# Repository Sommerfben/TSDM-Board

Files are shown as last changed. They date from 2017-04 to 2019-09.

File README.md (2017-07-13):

*Copyright UBC Formula Electric 2017.* 

*This documentation describes Open Hardware and is licensed under the CERN OHL v1.2.*

*You may redistribute and modify this documentation under the terms of the [CERN OHL v1.2](http://ohwr.org/cernohl). This documentation is distributed WITHOUT ANY EXPRESS OR IMPLIED WARRANTY, INCLUDING OF MERCHANTABILITY, SATISFACTORY QUALITY, AND FITNESS FOR A PARTICULAR PURPOSE. Please see the CERN OHL v1.2 for applicable conditions.*

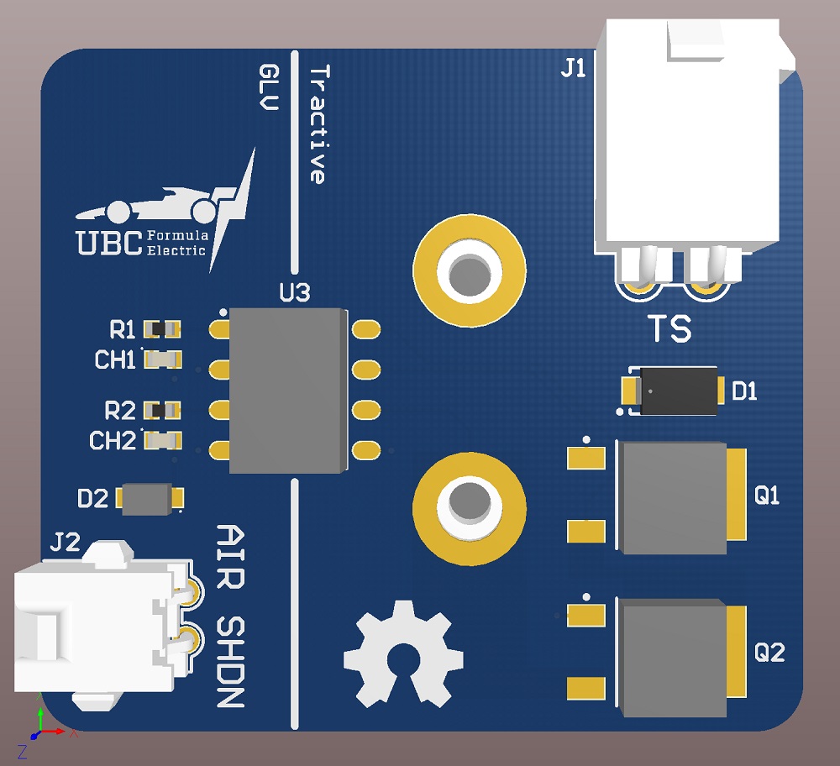
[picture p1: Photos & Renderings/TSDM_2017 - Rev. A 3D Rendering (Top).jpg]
TSDM_2017 - Rev. A 3D Render (Top)

*TSDM_2017 - Rev. A 3D Render (Top)*

# Overview

The Tractive System Discharge Module (TSDM_2017) discharges the tractive system in accordance with the 2017 Formula SAE rules. It uses two MOSFETs and a power resistor to discharge the repackaged inverter filtering capacitors below 60V in <1.5 seconds (to meet EV5.1.3). The power resistor is connected across the two poles of the tractive system whenever the AIR shutdown circuit is open, even when the vehicle is off.

# Features & Specifications

- The TSDM is separated into GLV (low-voltage) and tractive system (high-voltage) sections by a 10mm isolation boundary as per EV4.1.7. The GLV section contains the AIR shutdown circuit input and the tractive system section contains the MOSFETs and power resistor. The two halves are bridged by an optoisolated MOSFET driver.
- The board is mounted directly onto the power resistor using two M4 bolts. The power resistor is itself mounted to the inverter enclosure using two M3 studs and thermal compound. This design reduces the number of fasteners required for mounting and improves reliability by eliminating the use of additional wires and connectors.
- The AIR shutdown input uses a TE Micro MATE-N-LOK connector and is protected against reverse polarity by a Schottky diode and overcurrent by a PTC fuse. 
- The tractive system input uses a TE Mini-Universal MATE-N-LOK connector and is protected against reverse polarity by a 600V diode. Fusing is not allowed in the discharge circuit as per EV4.11.6.
- Each channel of the MOSFET driver has a red LED placed in series to provide a visual indicator of when the power resistor is disconnected from the tractive circuit.
- The power resistor is switched in and out of the system using two depletion-mode MOSFETs placed in series. The use of depletion-mode devices eliminates the need for conventional relays and allows the resistor to remain connected across the circuit when no power is applied to the system. The two MOSFETs are placed in series for redundancy, as a failure to discharge the tractive system quickly could pose a serious safety hazard when working on the vehicle.

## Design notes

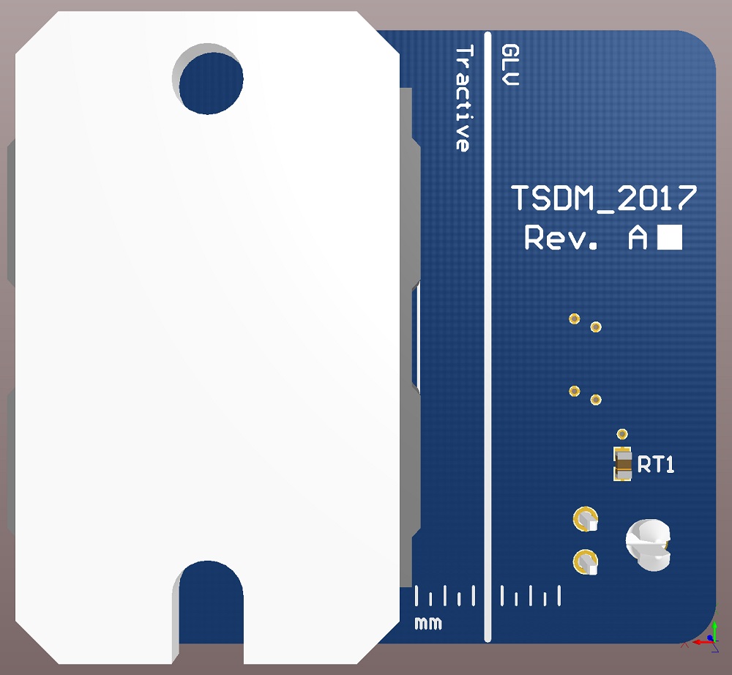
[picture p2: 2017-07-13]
Photos & Renderings/TSDM_2017 - Rev. A 3D Rendering (Bottom).jpg

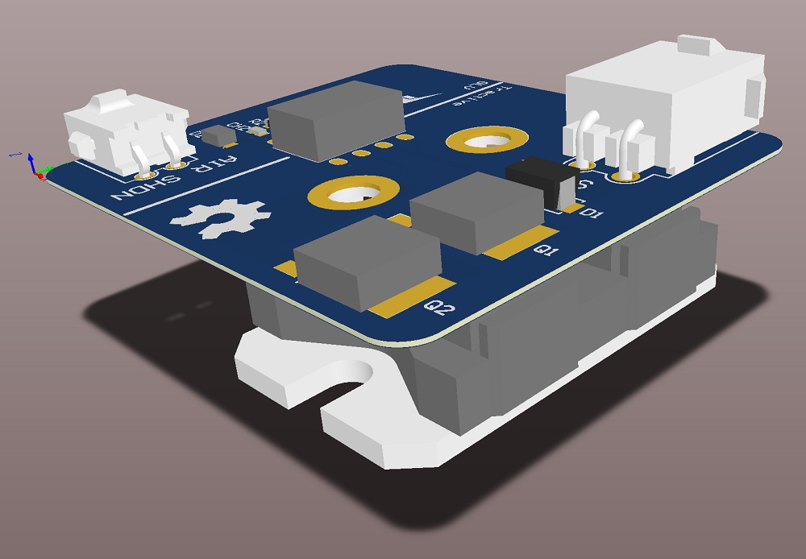
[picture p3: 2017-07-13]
Photos & Renderings/TSDM_2017 - Rev. A 3D Rendering (Isometric).jpg

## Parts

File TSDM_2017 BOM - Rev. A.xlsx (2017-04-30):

Description | Designator | Manufacturer | Manufacturer Part Number | Quantity | Supplier | Supplier Currency | Supplier Part Number | Supplier Order Qty | Supplier Unit Price | Supplier Subtotal
600V 1A Diode | D1 | STMicroelectronics (https://octopart-clicks.com/click/altium?sku=497-3765-1-ND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) | STTH1R06A (https://octopart-clicks.com/click/altium?sku=497-3765-1-ND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) | 1 | Digi-Key | CAD | 497-3765-1-ND (https://octopart-clicks.com/click/altium?sku=497-3765-1-ND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) | 1 | 0.65 | 0.65
60V 2A Schottky Diode | D2 | Nexperia USA Inc. (https://octopart-clicks.com/click/altium?sku=1727-2411-1-ND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) | PMEG6020AELRX (https://octopart-clicks.com/click/altium?sku=1727-2411-1-ND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) | 1 | Digi-Key | CAD | 1727-2411-1-ND (https://octopart-clicks.com/click/altium?sku=1727-2411-1-ND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) | 1 | 0.6 | 0.6
Green Chip LED | D3, D4 | Lite-On Inc. (https://octopart-clicks.com/click/altium?sku=160-1828-1-ND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) | LTST-C193KGKT-5A (https://octopart-clicks.com/click/altium?sku=160-1828-1-ND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) | 2 | Digi-Key | CAD | 160-1828-1-ND (https://octopart-clicks.com/click/altium?sku=160-1828-1-ND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) | 2 | 0.59 | 1.18
Mini-Universal MATE-N-LOK 2-Pin Female Connector | J1 | TE Connectivity AMP Connectors (https://octopart-clicks.com/click/altium?manufacturer=TE%20Connectivity%20AMP%20Connectors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) | 1-770966-0 (https://octopart-clicks.com/click/altium?manufacturer=TE%20Connectivity%20AMP%20Connectors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) | 1 | Digi-Key | CAD | A32471-ND (https://octopart-clicks.com/click/altium?manufacturer=TE%20Connectivity%20AMP%20Connectors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) | 1 | 1.27 | 1.27
Micro MATE-N-LOK 2-Pin Female Connector | J2 | TE Connectivity AMP Connectors (https://octopart-clicks.com/click/altium?manufacturer=TE%20Connectivity%20AMP%20Connectors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) | 2-1445055-2 (https://octopart-clicks.com/click/altium?manufacturer=TE%20Connectivity%20AMP%20Connectors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) | 1 | Digi-Key | CAD | A33207-ND (https://octopart-clicks.com/click/altium?manufacturer=TE%20Connectivity%20AMP%20Connectors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) | 1 | 1.11 | 1.11
500V Depletion-Mode N-MOSFET | Q1, Q2 | IXYS (https://octopart-clicks.com/click/altium?sku=IXTY1R6N50D2-ND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) | IXTY1R6N50D2 (https://octopart-clicks.com/click/altium?sku=IXTY1R6N50D2-ND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) | 2 | Digi-Key | CAD | IXTY1R6N50D2-ND (https://octopart-clicks.com/click/altium?sku=IXTY1R6N50D2-ND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) | 2 | 3.47 | 6.94
Thick Film Chip Resistor | R1, R2 | Panasonic Electronic Components (https://octopart-clicks.com/click/altium?manufacturer=Panasonic%20Electronic%20Components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) | ERJ-3EKF1001V (https://octopart-clicks.com/click/altium?manufacturer=Panasonic%20Electronic%20Components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) | 2 | Digi-Key | CAD | P1.00KHCT-ND (https://octopart-clicks.com/click/altium?manufacturer=Panasonic%20Electronic%20Components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) | 2 | 0.15 | 0.3
Thick Film Power Resistor | R3 | Ohmite (https://octopart-clicks.com/click/altium?sku=TGHLV1K00JE-ND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) | TGHLV1K00JE (https://octopart-clicks.com/click/altium?sku=TGHLV1K00JE-ND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) | 1 | Digi-Key | CAD | TGHLV1K00JE-ND (https://octopart-clicks.com/click/altium?sku=TGHLV1K00JE-ND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) | 1 | 69.85 | 69.85
Chip PTC Fuse | RT1 | Bel Fuse Inc. (https://octopart-clicks.com/click/altium?sku=507-1816-1-ND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) | 0ZCM0005FF2G (https://octopart-clicks.com/click/altium?sku=507-1816-1-ND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) | 1 | Digi-Key | CAD | 507-1816-1-ND (https://octopart-clicks.com/click/altium?sku=507-1816-1-ND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) | 1 | 0.22 | 0.22
Dual Photovoltaic MOSFET Driver | U3 | Broadcom Limited (https://octopart-clicks.com/click/altium?sku=516-3173-5-ND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) | ASSR-V621-302E (https://octopart-clicks.com/click/altium?sku=516-3173-5-ND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) | 1 | Digi-Key | CAD | 516-3173-5-ND (https://octopart-clicks.com/click/altium?sku=516-3173-5-ND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) | 1 | 6.2 | 6.2
 |  |  |  |  |  |  |  |  |  | 88.32

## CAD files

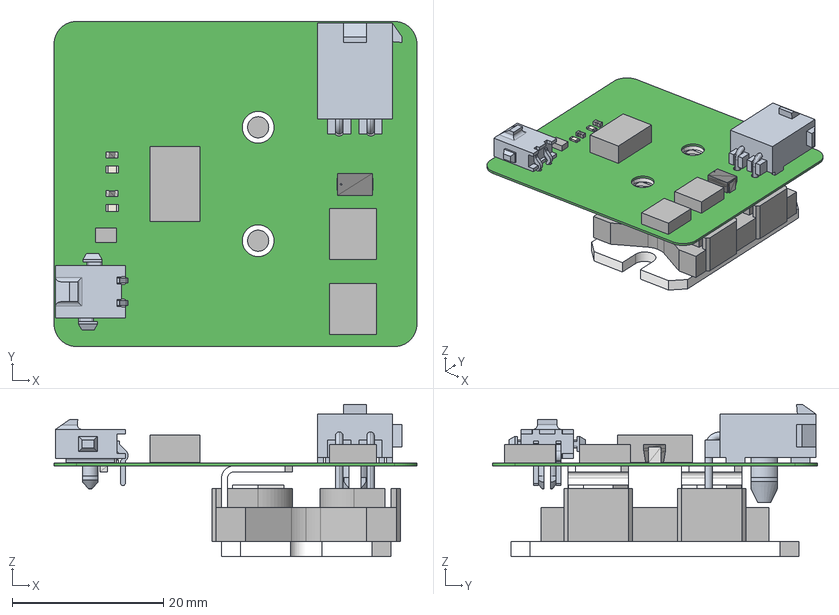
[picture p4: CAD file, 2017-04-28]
TSDM_2017 - Rev. A.step
48.0 x 43.0 x 20.2 mm
Board
User_Library-TGHLV10R0JEConfig__1
Extruded x 12
0ZCM
RC0603N x 2
c-2-1445055-2-b-3d
c-0770966-10-f-3d
SMA

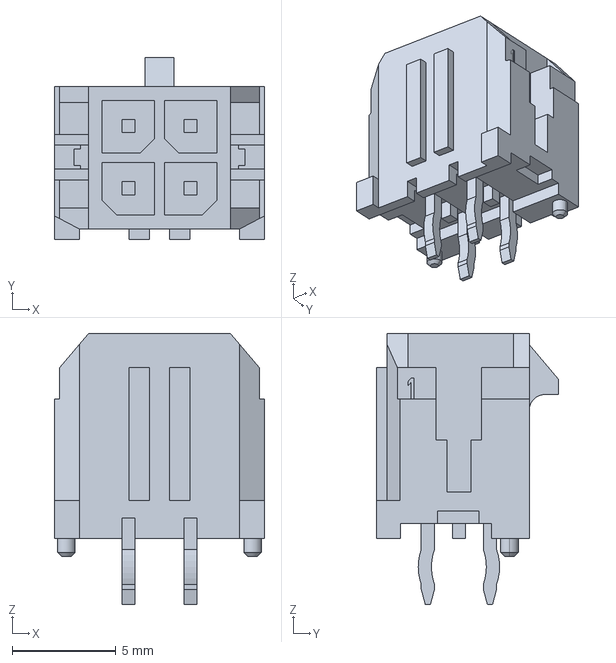
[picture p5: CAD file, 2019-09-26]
Altium/430450412.stp
10.2 x 8.77 x 13.1 mm

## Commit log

2016-10-18 Add empty Altium Designer 14.3 project
    [TSDM_2017.PcbDoc, TSDM_2017.PcbLib, TSDM_2017.PrjPcb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]
2016-10-18 [Libraries] Add components to schematic & PCB libraries
    - Avago ASSR-V621-302E
    - Lite-On LTST-C193K-Series
    - Panasonic ERJ-Series
    - TE 1-770966-0
    - TE 2-1445055-2
    [TSDM_2017.PcbLib, TSDM_2017.SchLib]
2016-11-08 [Datasheets] Add TGH Series 200W Resistor datasheet
2016-11-08 [Datasheets] Rename TGH Series 200W Resistor datasheet
2016-11-27 [Libraries] Add TGHLV1K00JE, IXTP1R6N50D2 to schematic and PCB libraries [PCB]FFirst PCB draft[Datasheets] Add reference for mounting TGHLV1K00JE and for using IXTP1R6N50D2 and IXTP1R6N50D2 [SETP] Ad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
    [TSDM_2017.CSV, TSDM_2017.PcbDoc, TSDM_2017.PcbLib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]
2016-11-27 [PCB] Add UBC Formula Electric PCB rules file
    [TSDM_2017.CSV]
2017-02-05 [PCB] Removed mounting holes and changed resistor to the other board side
    [TSDM_2017.PcbDoc, TSDM_2017.PcbLib, TSDM_2017.PrjPcb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]
2017-02-05 [PCB] Minor designator and trace modifications
    [TSDM_2017.PcbDoc]
2017-02-07 [Libraries] Clean up schematic & PCB libraries
    [TSDM_2017.PcbLib, TSDM_2017.SchLib]
2017-02-07 [Schematic] Clean up schematic
    [TSDM_2017.SchDoc]
2017-02-07 Remove unused Altium files
    [User Library-TGHLV10R0JEConfig_ 1.STEP]
2017-02-07 [References] Add reference document
    - AN-500 - Depletion-Mode Power MOSFETs and Applications
2017-02-11 [PCB] Added LEDs for MOSFET driver and protection diodes for connectors
    [TSDM_2017.PcbDoc, TSDM_2017.PcbLib, TSDM_2017.PrjPcb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]
2017-02-11 [PCB] Minor placement changes
    [TSDM_2017.PrjPcb]
2017-02-11 [Schematic] Change font type and font size [PCB] Remove unneeded vias
    [TSDM_2017.PcbDoc, TSDM_2017.SchDoc]
2017-02-13 [Libraries] Add component footprints to PCB library
    - NXP PMEG6020AELRX
    - STMicroelectronics STTH1R06
    [TSDM_2017.PcbLib]
2017-02-13 [Schematic] Add supplier links to all components
    [TSDM_2017.SchDoc]
2017-02-13 [Schematic] Modify LED resistor values
    [TSDM_2017.SchDoc]
2017-02-13 [Libraries] Add thermistor to schematic & PCB libraries
    [TSDM_2017.PcbLib, TSDM_2017.SchLib]
2017-02-13 [Schematic] Add PTC fuse to AIR_SHDN circuit
    [TSDM_2017.SchDoc]
2017-02-13 [PCB] Add PTC fuse to PCB
    [TSDM_2017.PcbDoc]
2017-02-13 [PCB] Route PTC fuse [Schematic] Fix power resistor pin names
    [TSDM_2017.PcbDoc, TSDM_2017.SchDoc]
2017-02-13 [PCB] Change board size
    [TSDM_2017.PcbDoc, TSDM_2017.SchDoc]
2017-04-28 [PCB] Modify board layout
    - Modify layout to fit inside repackaged inverter
    [TSDM_2017.PcbDoc]
2017-04-28 [PCB] Export Rev. A Gerber files
    [TSDM_2017.GBL, TSDM_2017.GBO, TSDM_2017.GBP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]
2017-04-28 [Libraries] Add 3D models to components
    [TSDM_2017.PcbDoc, TSDM_2017.PcbLib, TSDM_2017.PrjPcb]
2017-04-28 [PCB] Export 3D STEP file of Rev. A board
    [TSDM_2017 - Rev. A.step]
2017-04-30 [Schematic] Check and update supplier links
    [TSDM_2017.SchDoc]
2017-04-30 [Schematic] Fix broken document links
    [TSDM_2017.SchDoc]
2017-04-30 [BOM] Export Rev. A bill of materials
    [TSDM_2017 BOM - Rev. A.xlsx]
2017-07-13 [Media] Add 3D renderings of Rev. A board
2017-07-13 [Media] Convert 3D board renderings from PNG to JPEG
2017-07-13 [README] Add 3D render of Rev. A board
2019-09-26 [Schematic] Add MOLEX 4-pin header
    [430450412.stp, TSDM_2017.PcbLib, TSDM_2017.PrjPcb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]
2019-09-28 [Schematic] Added Molex 4-pin header to TSDM schematic
    [TSDM_2017.SchDoc, TSDM_2017.SchLib]
